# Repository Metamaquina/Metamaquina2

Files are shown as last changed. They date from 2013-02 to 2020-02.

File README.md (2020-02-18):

Metamaquina2
============

Metamaquina 2 - fully parametric 3D printer

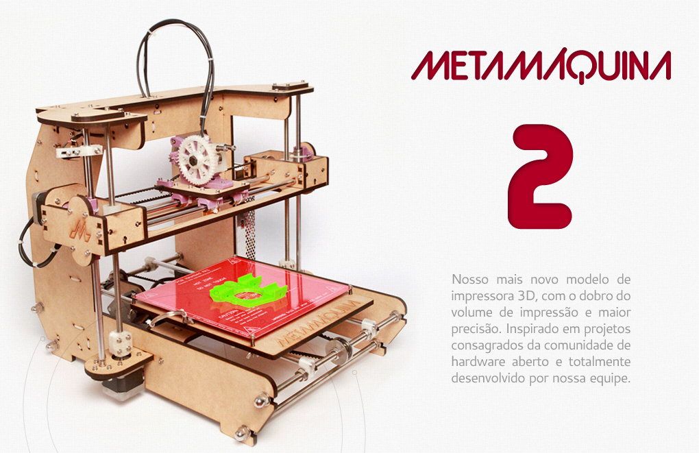
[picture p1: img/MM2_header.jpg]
A photo of the Metamaquina 2 desktop 3d printer


Manufacturing Instructions
==========================

This is a 3d printer project that is completely designed using the parametric CAD tools
 provided by OpenSCAD. In order to deal with this source code you'll need to install OpenSCAD,
following the instructions at: www.openscad.org

The main structure of the machine is built using lasercut MDF panels. The curves for lasercutting 
can be exported to DXF by rendering the lasercutter_6mm_MDF.scad file. Open it in OpenSCAD, press F6 (to compile) and then click Design->Export DXF. The resulting DXF file can be used to cut 6mm thick MDF sheets (or you can change the thickness in the source if you plan to work with some other materials but be sure to review the 3d model in this case since some parts of the design depend on 6mm thickness).

There is also a panel for lasercutting 2mm acrylic to cover the electronics PCB and a panel for lasercutting 5mm acrylic for the ZMAX/ZMIN endstop holders and a couple of 5mm spacers for the LCExtruder. There can be generated from the lasercutter_2m_acrylic.scad and lasercutter_5m_acrylic.scad, respectively. 

Laser Cutter Panel #1
Laser Cutter Panel #2
Laser Cutter Panel #3

The complete 3D model of the machine is described by the Metamaquina2.scad file. Open is in 
OpenSCAD and press F5 to render it.

An OpenSCAD rendering of the Metamaquina 2 desktop 3d printer

Hacking the code
================
Feel free to send us pull requests at https://github.com/Metamaquina/Metamaquina2
 if you make any change to this design that you consider worth sharing with us.

happy hacking,

Felipe Sanches

R&D director at Metamaquina.com.br

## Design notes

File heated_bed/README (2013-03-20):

This is a heated bed design developed in KiCAD.

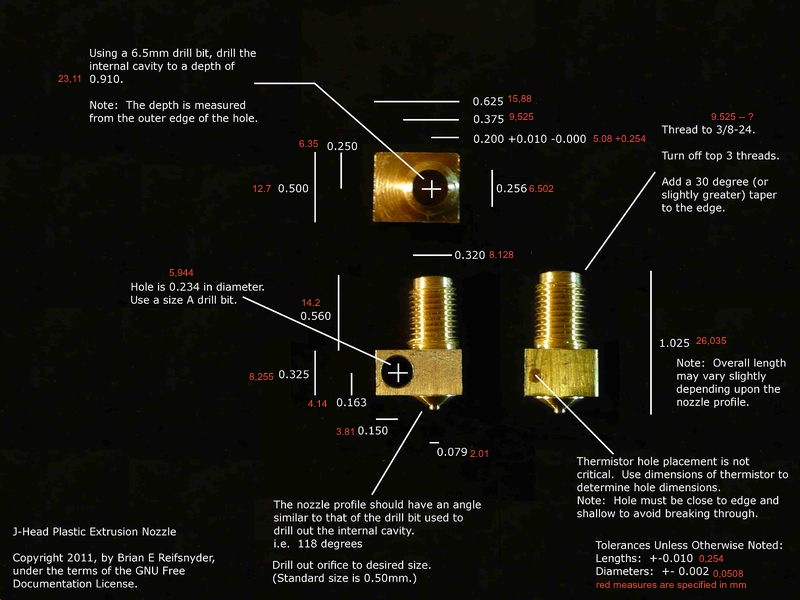
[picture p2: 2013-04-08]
doc/Jhn_md_brass_heater_nozzle.jpg

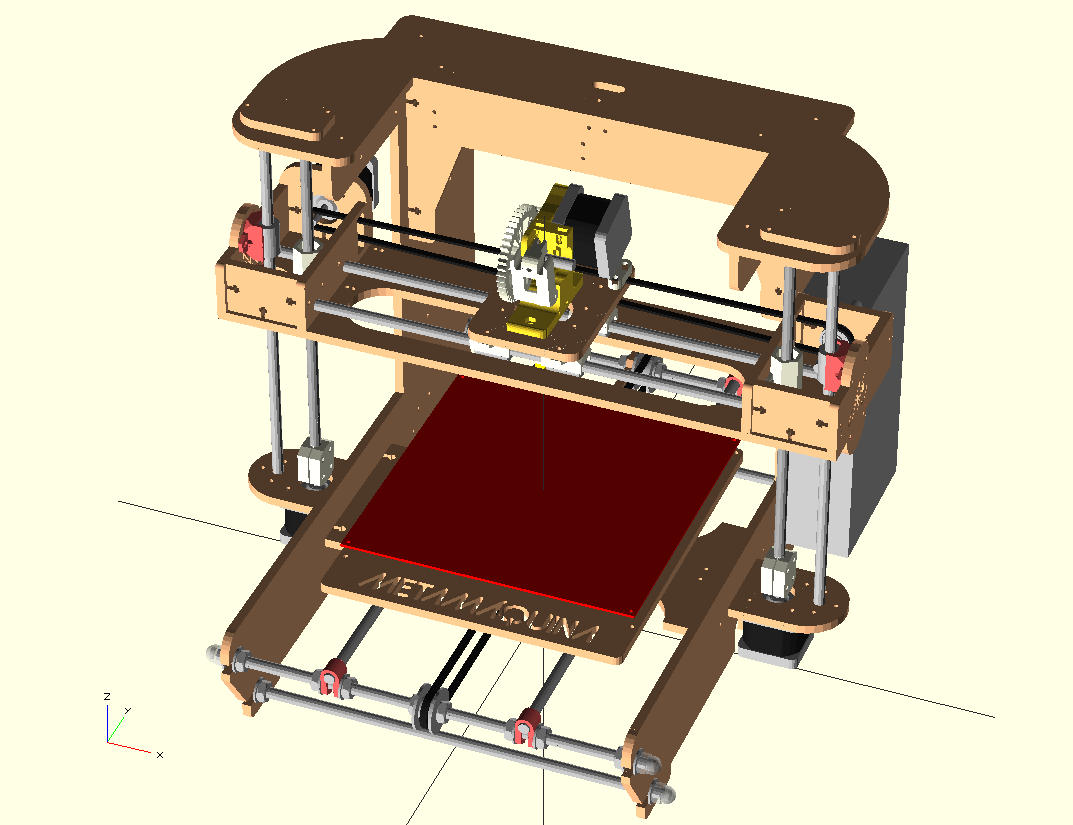
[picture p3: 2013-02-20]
img/MM2.png

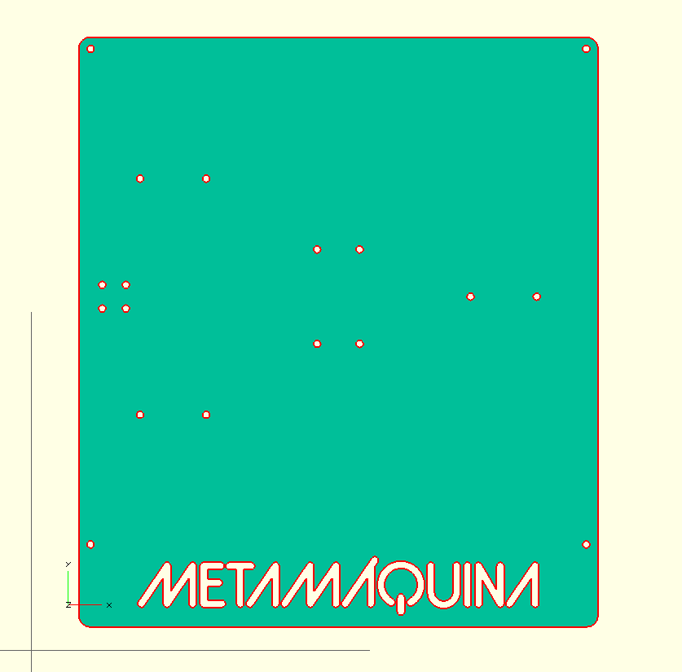
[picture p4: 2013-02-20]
img/lasercutter_panel3.png

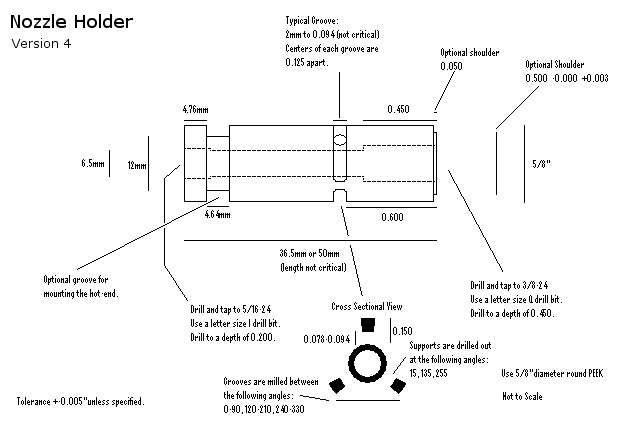
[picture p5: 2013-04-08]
doc/Jhn_nozzle_holder_v4.jpg

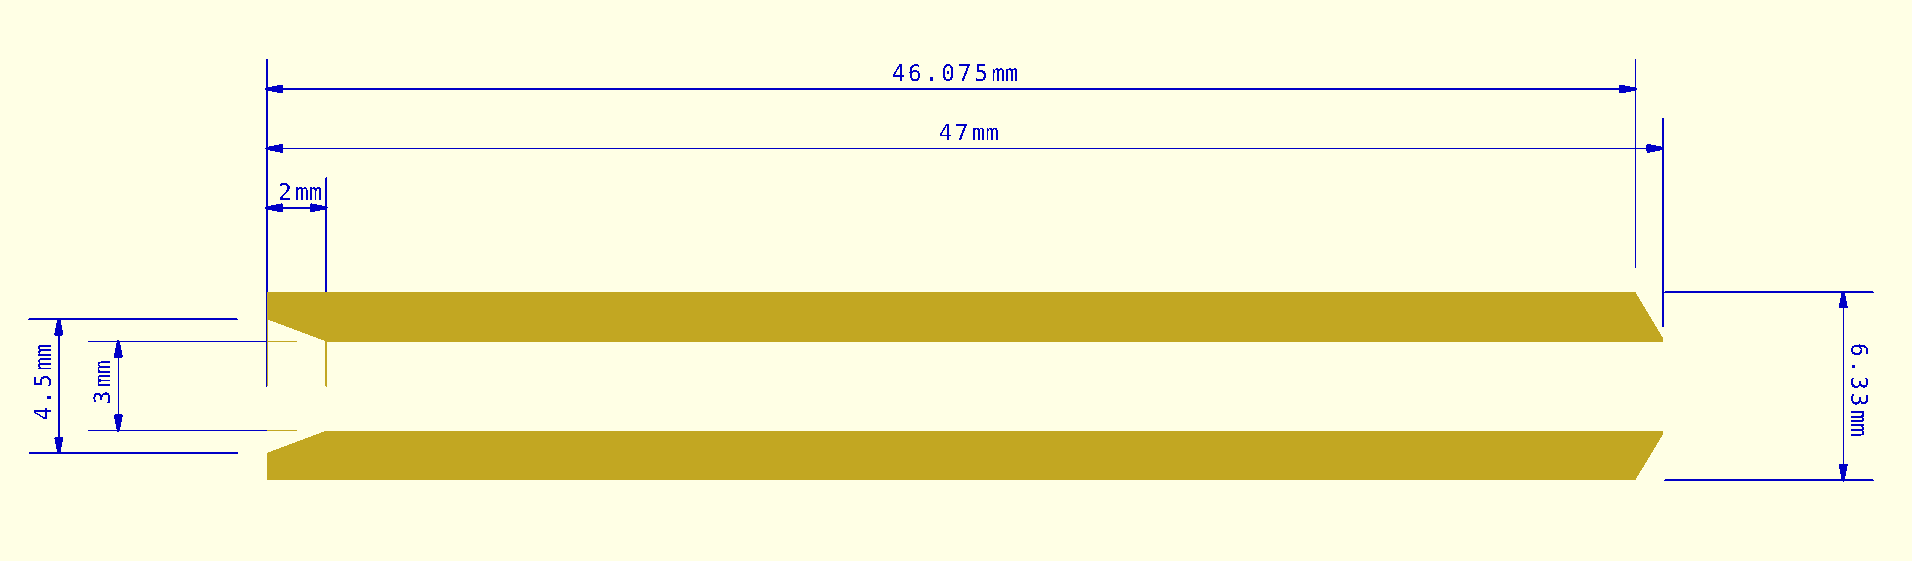
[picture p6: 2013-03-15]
doc/ptfe_liner.png

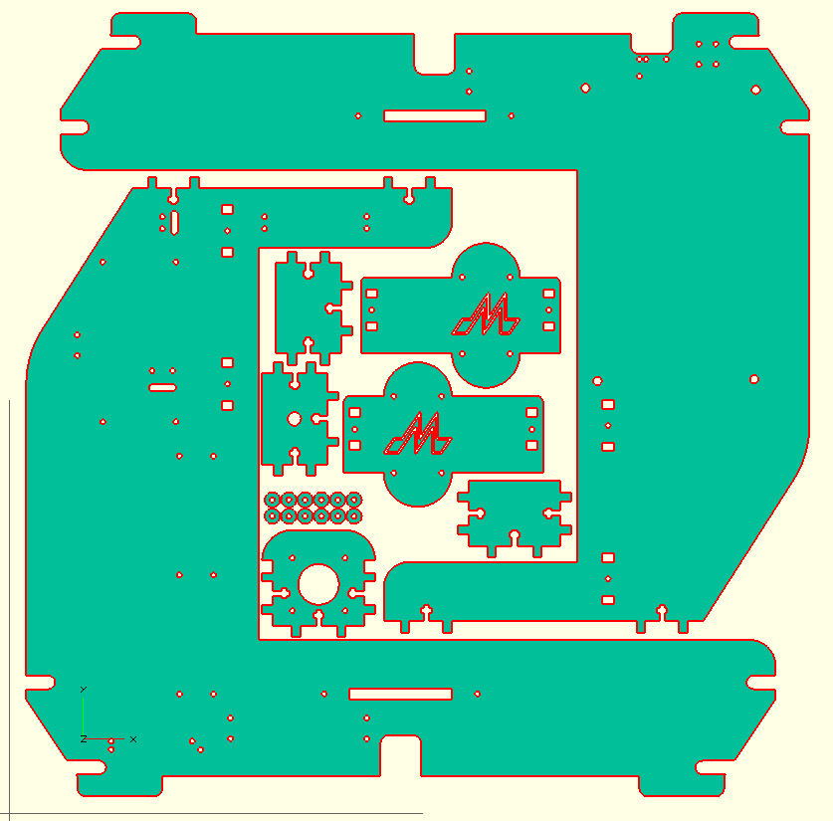
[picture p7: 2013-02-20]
img/lasercutter_panel1.png

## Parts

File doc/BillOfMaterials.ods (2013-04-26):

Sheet: Peças metálicas
Metamáquina 2 – Bill Of Materials |  |  |  | Incomplete
Peças metálicas |  | Local | Quantidade
Barras
 | Lisas M8 | eixo X (420 mm) | 2
 |  | eixo Y (442 mm) | 2
 |  | eixo Z (309 mm) | 2
 |  | Total | 6
 | Roscadas M8 | eixo Z (285 mm) | 2
 |  | Horizontais (309 mm) | 4
 |  | Total | 6
Rolamentos
 | LM8UU | carro X | 4
 |  | carro Y | 3
 |  | X-end idler | 2
 |  | X-end motor | 2
 |  | Total | 11
 | 608ZZ
 |  | Total
Parafusos
 |  | Total | 0
Motores
 | Motor de passo NEMA 17 2,5 kgf |  | 5
 |  | Total | 5
Porcas
 | M2.5 mm |  | 2
 |  | Total
 | M3
 |  | Total | 0
 | M3 locknut
 |  | Total | 0
 | M4
 |  | Total | 0
 | M8
 |  | Total | 0
 | M8 locknut
 |  | Total | 0
 | M8 cap nut
 |  | Total | 0
Molas
 |  | Total | 0
Arruelas
 | M3
 | M4
 | M8
 |  | Total | 0

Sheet: Peças de madeira
Metamáquina 2 – Bill Of Materials |  |  |  | Incomplete
Peças de madeira |  | Local | Quantidade
Espaçadores
 | Total |  | 50
Plataforma X |  |  | 1
Plataforma Y |  |  | 1
Endstops
 | Z |  | 1
 | Y |  | 2
 | X
 | Total |  | 3
Endstop holder

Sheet: Peças plásticas
Metamáquina 2 – Bill Of Materials |  |  |  | Incomplete
Peças plásticas |  | Local | Quantidade
Bar clamp
 |  | Eixo Y | 4
 |  | Total | 4
Clipes autoadesivos
 | RA6 | Painel esquerdo | 1
 |  | Total | 1
 | RA13 | Painel esquerdo | 7
 |  | Painel direito | 2
 |  | Painel superior | 1
 |  | Painel inferior | 3
 |  | Total | 13
Correias
 | GT2 x 5mm | Eixo X | 1
 |  | Eixo Y | 1
 |  | Total | 2
Engrenagens
 | Grande | Extrusor | 1
 | Pequena | Extrusor | 1
 |  | Total | 2
Z-link
 |  | Eixo Z | 2
 |  | Total | 2

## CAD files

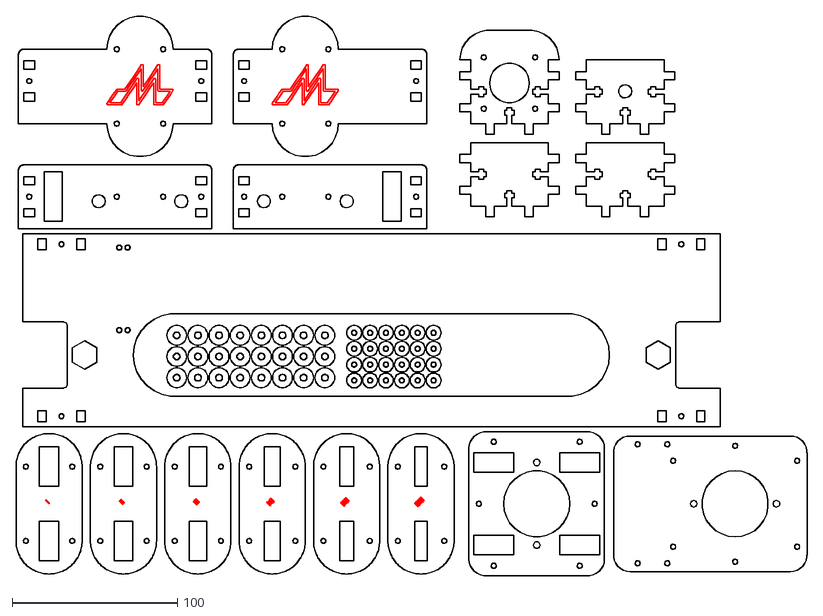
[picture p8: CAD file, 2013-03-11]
dxf/sandwich_test_panel_06Mar2013.dxf
478.5 x 338.4

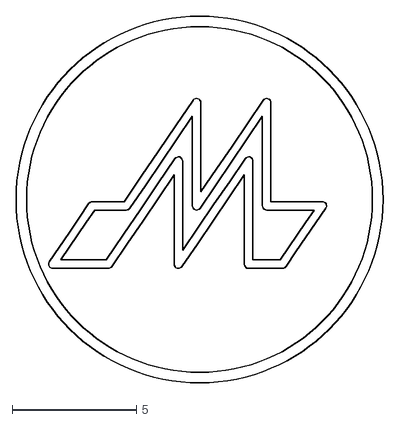
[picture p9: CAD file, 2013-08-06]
M_circle.dxf
14.8 x 14.8

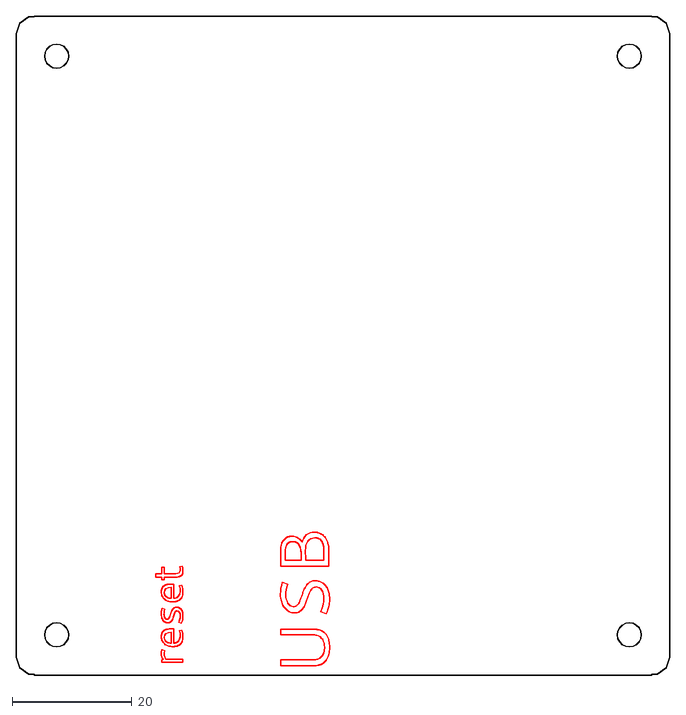
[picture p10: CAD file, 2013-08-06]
lasercutter_2mm_acrylic.dxf
109.0 x 110.0

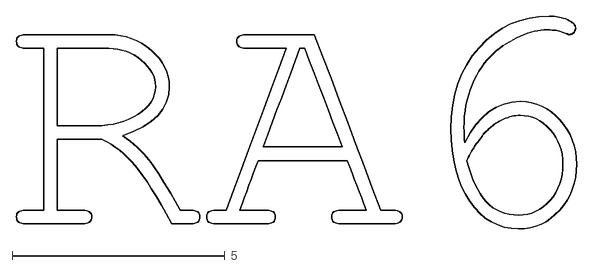
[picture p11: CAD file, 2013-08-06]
RA6.dxf
13.2 x 5.00

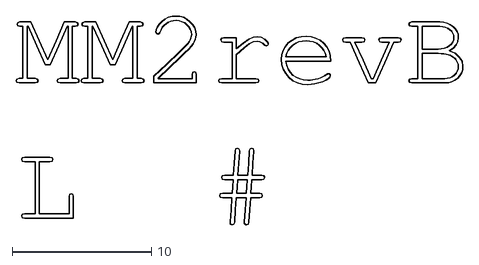
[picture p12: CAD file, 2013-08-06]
serial_number_template.dxf
32.1 x 15.0

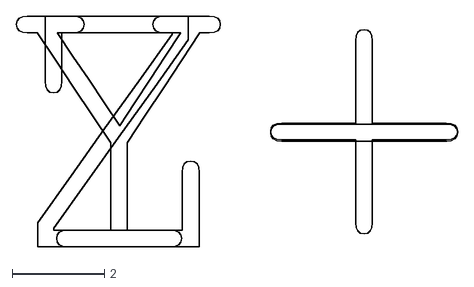
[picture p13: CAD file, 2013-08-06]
labels.dxf
9.56 x 5.00

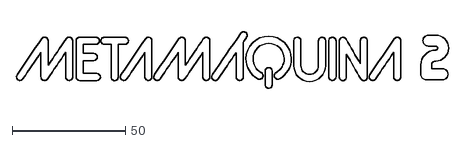
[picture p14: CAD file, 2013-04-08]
metamaquina-2.dxf
191.0 x 24.9

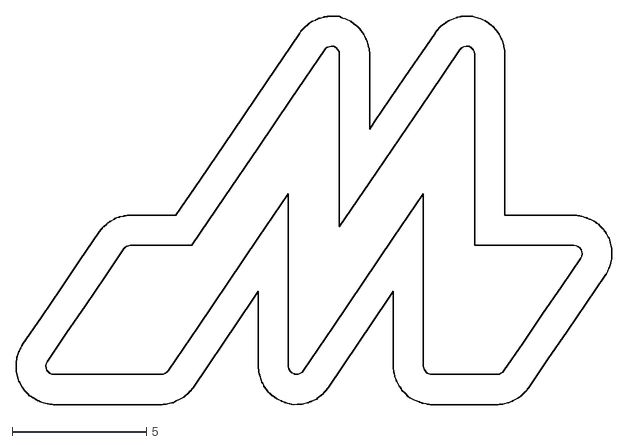
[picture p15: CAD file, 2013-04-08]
MM_hole.dxf
22.2 x 14.4

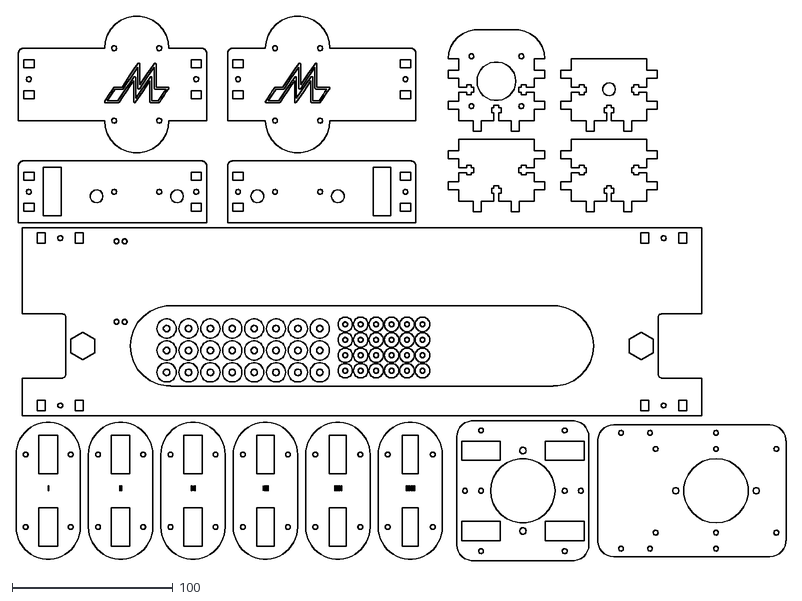
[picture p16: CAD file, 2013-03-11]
sandwich_test_panel.dxf
478.5 x 338.4

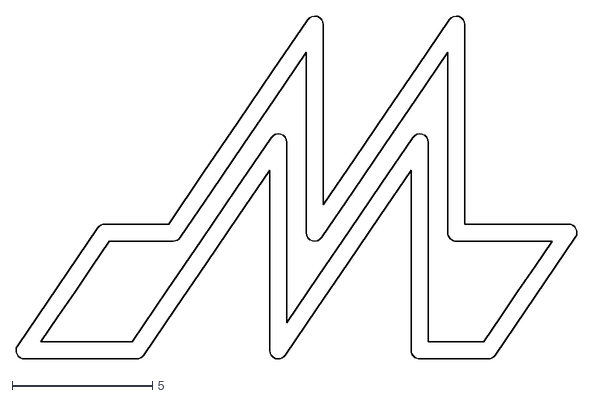
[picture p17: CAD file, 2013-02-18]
MM_logo_small.dxf
20.0 x 12.2

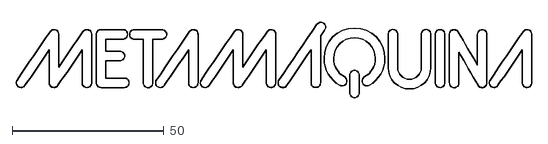
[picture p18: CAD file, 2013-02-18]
metamaquina-170mm_X_25mm.dxf
169.9 x 24.9

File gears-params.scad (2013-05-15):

// (c) 2013 Metamáquina <http://www.metamaquina.com.br/>
//
// Author:
// * Felipe C. da S. Sanches <fsanches@metamaquina.com.br>
//
// This program is free software: you can redistribute it and/or modify
// it under the terms of the GNU General Public License as published by
// the Free Software Foundation, either version 3 of the License, or
// (at your option) any later version.
//
// This program is distributed in the hope that it will be useful,
// but WITHOUT ANY WARRANTY; without even the implied warranty of
// MERCHANTABILITY or FITNESS FOR A PARTICULAR PURPOSE.  See the
// GNU General Public License for more details.
//
// You should have received a copy of the GNU General Public License
// along with this program.  If not, see <http://www.gnu.org/licenses/>.

gear_thickness = 10;

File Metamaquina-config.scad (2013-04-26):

/*Thickness of acrylic or plywood sheets to use.*/
thickness = 6; //millimiters

/*This value is added to the thickness value when drawing cuts for connecting perpendicular sheets together*/
slot_extra_thickness = 0.5;

module TSlot_holes(width=50){
  t_slot_holes(width=width, thickness=thickness+slot_extra_thickness);
}

module TSlot_joints(width=50){
  t_slot_joints(width=width, thickness=thickness, joint_size=5);
}

/*z motor placement in the original Prusa was on top. Our design uses the z motors in the bottom of the machine, but if you want them on top, you can set this variable to true. */
zmotors_on_top = false;

/* Desired build volume: */
BuildVolume_X=200;
BuildVolume_Y=200;
BuildVolume_Z=150;

//rendering configs:
render_lasercut=true;
render_pcb=true;
render_ABS=true;
render_PLA=true;
render_metal=true;
render_threaded_metal=true;
render_rubber=true;
render_peek=true;
render_nylon=true;
render_acrylic=true;

render_nozzle=true;
render_powersupply=true;
render_calibration_guide = false;
render_build_volume=false;
render_xplatform=true;
render_bolts = false; //work-in-progress
render_extruder = true;

//Colors
dark_green = [0,0.2,0];
rubber_color = [0.1, 0.1, 0.1];
nozzle_color = "gold";
pcb_color = [1.0, 0.0, 0.0];
threaded_metal_color = [0.6, 0.6, 0.6];
metal_color = [0.7, 0.7, 0.7];
powersupply_color = metal_color;
PLA_color = [0.95, 0.35, 0.35];
ABS_color = [0.95, 0.95, 0.85];
//sheet_color = [0.95, 0.8, 0.65];
sheet_color = [227/230, 190/230, 151/230];
//sheet_color = [0.9, 0.3, 0.3, 1];
peek_color = "beige";
dark_grey = [0.3, 0.3, 0.3];
green_plastic_color = [0.7,0.8,0,7];
black_plastic_color = [0.3,0.3,0.3];

epsilon=0.1;
inch=25.4;
m25_diameter = 2.5;
m3_diameter = 3;
m4_diameter = 4;
m8_diameter = 8;

//-------------------------
//RepRap standards:

X_rods_distance = 50;
X_rods_diameter=8;
z_rod_z_bar_distance = 30;
Y_rods_distance = 140;

//-------------------------
extruder_mount_holes_distance = X_rods_distance + 14;
microswitch_holes_distance = 9.4;
endstop_holder_width = 15;//TODO
endstop_holder_height = 8;//TODO

XPlatform_height = 45;

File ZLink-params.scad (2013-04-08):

dx_z_threaded = 14;
ZLink_rod_height = 11*sqrt(3)/2;
Zlink_hole_height = (XPlatform_height-thickness)/3;

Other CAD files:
font.dxf
CalibrationRules-conf.scad
608zz_bearing.scad
CalibrationRules.scad
CalibrationZBars.scad
FilamentSpoolHolder.scad
Metamaquina2.scad
Metamaquina_2_extruders.scad
NEMA-dimensions.scad
NEMA.scad
PTFE_liner.scad
PowerSupply.scad
RAMBo.scad
ZLink.scad
acrilico_5mm.scad
bar-clamp.scad
belt-clamp.scad
bolts.scad
cable_clips.scad
configuration.scad
coupling.scad
detailed_608zz_bearing.scad
domed_cap_nuts.scad
endstop.scad
functions.scad
gears.scad
gears_Bowden.scad
heated_bed.scad
hobbed_bolt.scad
jhead.scad
jheads.scad
large_extruder_gear.scad
lasercut_2_extruders.scad
lasercut_extruder.scad
lasercutter_5mm_acrylic.scad
lasercutter_6mm_MDF.scad
lasercutter_6mm_MDF_CalibrationRules.scad
lasercutter_6mm_MDF_CalibrationZBars.scad
lasercutter_6mm_MDF_SpoolHolder.scad
lasercutter_panel.scad
lasercutter_panel4.scad
lasercutter_panel5.scad
lm8uu_bearing.scad
metric.scad
mm2logo.scad
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

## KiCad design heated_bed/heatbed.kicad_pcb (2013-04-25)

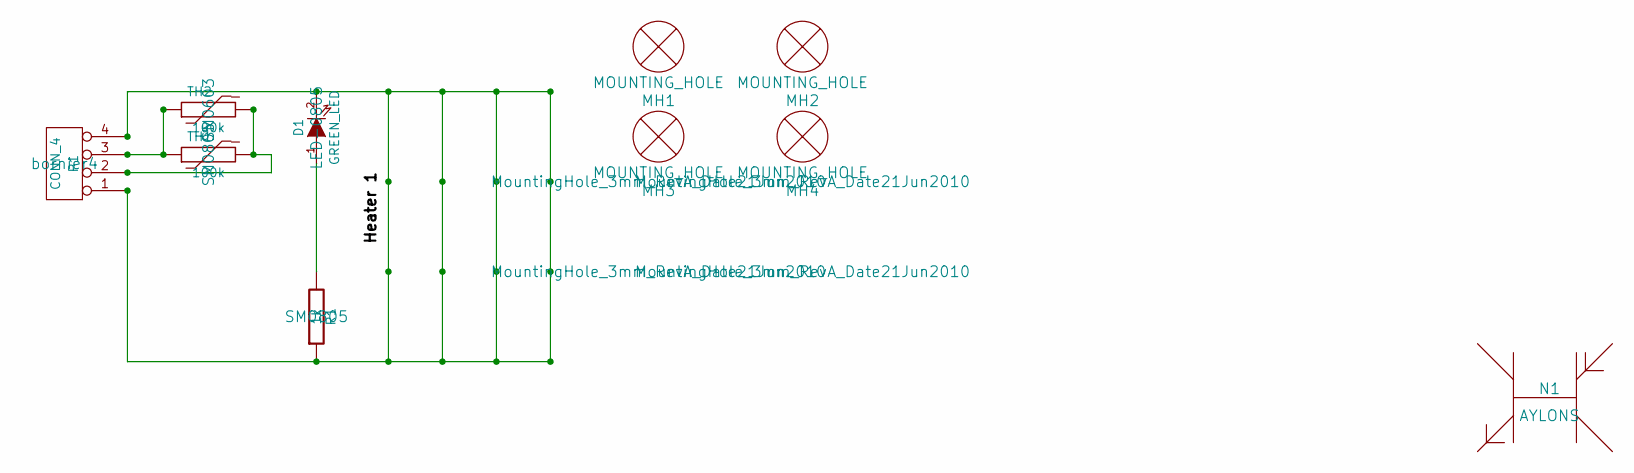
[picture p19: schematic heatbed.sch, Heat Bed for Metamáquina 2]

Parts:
D1: GREEN_LED; LED-0805
MH1, MH2, MH3, MH4: MOUNTING_HOLE; MountingHole_3mm_RevA_Date21Jun2010
N1: AYLONS
P1: CONN_4; bornier4
R1: 1k; SM0805
TH1: 100k; SM0805
TH2: 100k; SM0603

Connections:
unnamed: P1.3, TH1.1, TH2.1
unnamed: P1.2, TH1.2, TH2.2
unnamed: D1.1 (A), R1.2
unnamed: D1.2 (K), P1.1, P1.4, R1.1

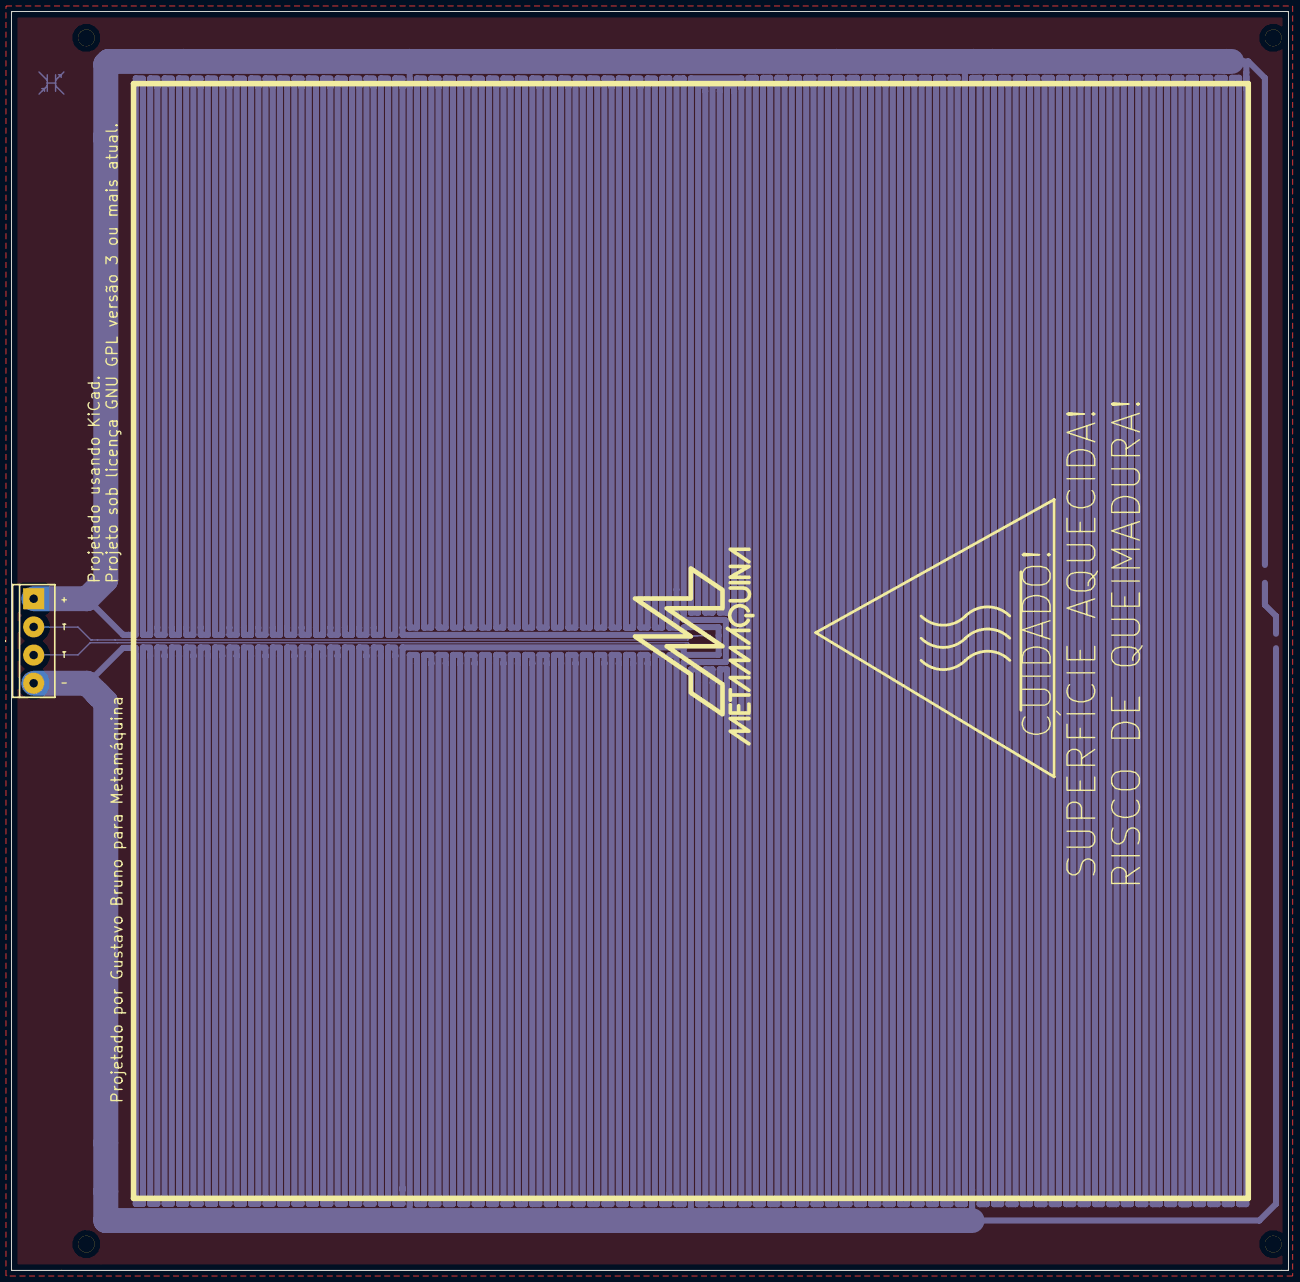
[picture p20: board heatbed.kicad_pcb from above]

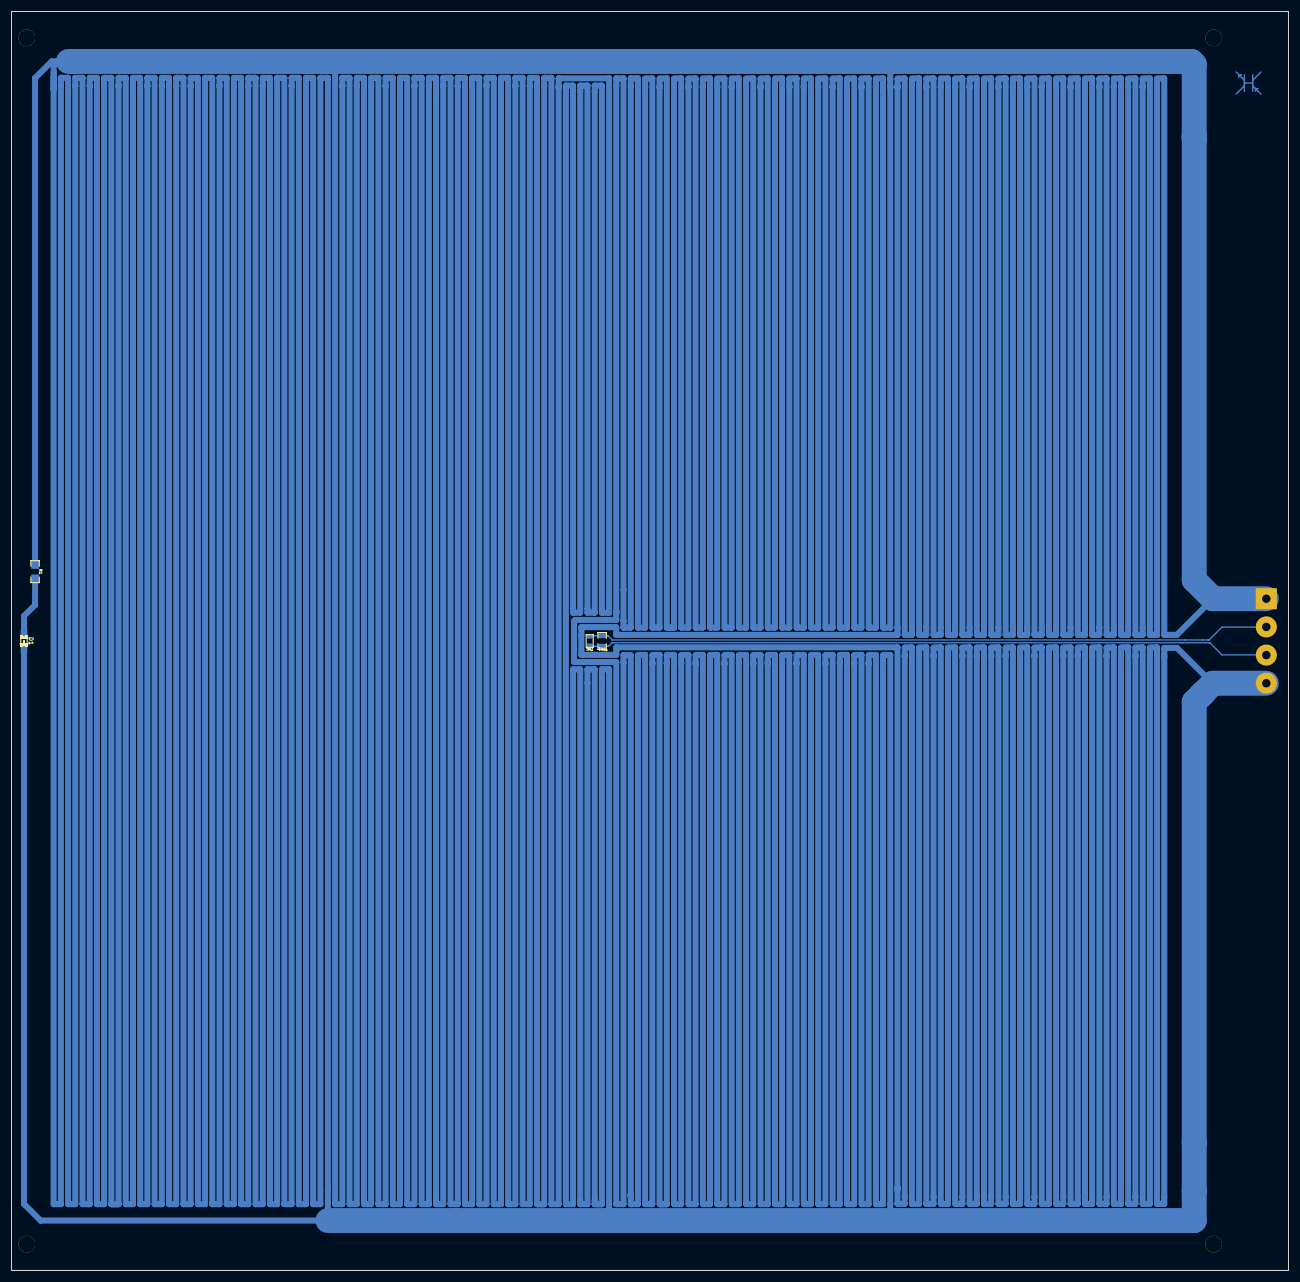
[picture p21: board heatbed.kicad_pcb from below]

Board: 2 copper layers, 230.2 x 227.0 mm, 10 parts (4 on the bottom side), 4 nets.

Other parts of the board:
VAL: MM_logo

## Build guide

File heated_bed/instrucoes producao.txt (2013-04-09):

O funcionamento correto desta placa depende da resistência das suas trilhas. Portanto:

* A placa DEVE ter densidade de cobre de 1oz.
* A placa NÃO deve passar por eletrodeposição ANTES da máscara de solda.

Outras informações:
* Os pads devem ser metalizados por HAL.
* A camada da frente não tem conexão elétrica com nenhuma trilha. Sua função é distribuir calor, portanto a placa deve ser 2 camadas, como nos gerbers.
* Não é necessário metalizar os furos, nem os do conector.

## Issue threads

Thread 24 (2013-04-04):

validar termistor do bico

felipesanches, 2013-04-04:
- Carregar tabela adequada de termistores para o modelo novo de term. e testar de 26 a 240 graus celsius ligado a um bico de extrusão e comparando com o termopar

felipesanches, 2015-02-12:
Tarefa concluída em 2013.

Closed 2015-02-12.

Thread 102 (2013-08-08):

Furo no carro X

rodrigopitanga, 2013-08-08:
O furo para fixação do extrusor no carro X voltado para a parte de trás deve ser uma fenda, e não um furo.

Isso permitirá que o parafuso M4x25 seja fixado na porca antes de o motor ser colocado no bloco extrusor, o que facilitaria muito a montagem do extrusor no carro posteriormente.

felipesanches, 2015-02-12:
foi implementado na revisão D

Closed 2015-02-12.

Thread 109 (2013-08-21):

Bloco extrusor esquenta demais e derrete/esmaga filamento

rodrigopitanga, 2013-08-21:
Causando emplastamento.

Solução: baixar corrente do motor e diminuir pressão na mola do idler.

felipesanches, 2015-02-12:
correção implementada em 2013

Closed 2015-02-12.

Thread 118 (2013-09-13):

Cabeamento do cabeçote extrusor fica muito próximo do motor da extrusora

gui7vaz, 2013-09-13:
Hj coloquei a mão na fiação e não dava nem para encostar o dedo de tão quente.
Isso pode ser um perigo. Vou até fazer um seguro pro meu apartamento.
Soltei um pouco os cabos de modo que eles ficassem bem distantes do motor.

felipesanches, 2015-02-12:
O super-aquecimento dos motores do extrusor foram corrigidos em 2013. Tratava-se de uma configuração errada de corrente do driver de motor de passo.

Closed 2015-02-12.

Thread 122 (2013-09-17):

As peças ficam deformadas na "parte de trás"

gui7vaz, 2013-09-17:
Ando imprimindo algumas coisas e percebi que a parte de trás das peças sempre ficam um pouco deformada. Ontem coloquei a mão na parte traseira da impressora e realmente tinha uma massa de ar quente lá. Hoje farei alguns testes colocando um ventilador virado para o local.

felipesanches, 2015-02-12:
issue duplicada

Closed 2015-02-12.

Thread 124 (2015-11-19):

Dependencia urlgrabber ausente da documentacao

rodrigopitanga, 2015-11-19:
apt-get install python-urlgrabber

felipesanches, 2015-11-19:
Tenho a impressão de que você cadastrou essa issue no repositório errado. Me parece que você queria ter cadastrado isso no repo do Pronterface / Printrun

felipesanches, 2015-11-19:
de qualquer modo, consertei isso no README.md do nosso Printrun agora (no branch mm2)

rodrigopitanga, 2015-11-19:
Ok. Precisa consertar na doc do site tb.

Em 19 de novembro de 2015 18:13:03 BRST, "Felipe Corrêa da Silva Sanches" <notifications@github.com> escreveu:
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

--
Sent from my Android device with K-9 Mail. Please excuse my brevity.

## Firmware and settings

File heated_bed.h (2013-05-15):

// (c) 2013 Metamáquina <http://www.metamaquina.com.br/>
//
// Author:
// * Felipe C. da S. Sanches <fsanches@metamaquina.com.br>
//
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
use <heated_bed.scad>;

heated_bed_pcb_thickness = 2;
heated_bed_pcb_width = 227;
heated_bed_pcb_height = 224;
heated_bed_glass_thickness = 3;

glass_w=heated_bed_pcb_width;
glass_h=200; //TODO

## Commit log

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2013-02-18 Adding a volumetric representation of the space taken by the RAMBo electronics.
    [Metamaquina2.scad]
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2013-02-19 calculate machine dimentions based on the actual desired max build volume (previously we were using the heated bed pcb dimensions as our reference parameter)
    [Metamaquina2.scad]
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2013-02-19 tweak RAMBo y position to align to the top of the power supply
    [Metamaquina2.scad]
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2013-02-21 Initial commit for heatbed hardware design.
    Created schematics, associated components to its footprint (dummy in case of PCB traces and undecided footprints) and generated a PCB layout file.
    [heatbed.sch]
2013-02-21 Created Kicad project and designed the first schematic for the heated bed. Also, associated componentes with footprints (dummy in some cases) and generated the board layout file.
    [heatbed.sch]
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2013-02-27 3d model / 2d drawing of the PTFE liner for our hotend
    [PTFE_liner.scad]
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2013-03-04 Feita a primeira metade da PCB, com duas trilhas de aquecimento prontas. Restam as duas trilhas com menos interferencia externa
    [heatbed.kicad_pcb, heatbed.sch]
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2013-03-06 test panel sent to prototyping on the laser cutter on march 6th 2013 purpose: to validate the bearing sandwich design pattern and to choose the best value for the sandwich_tightening parameter
    [Metamaquina2.scad, sandwich_test_panel.dxf, sandwich_test_panel_06Mar2013.dxf]
2013-03-06 source code for the test panel mentioned in the previous commit message
    [sandwich_test_panel.scad]
2013-03-07 invert position of ybearings to avoid hitting the ymotor
    [Metamaquina2.scad]
2013-03-08 Removing 3d printable wade extruder from the design. We'll try using an extruder based on the Printrbot one, so that we can lasercut it.
    [MM_wade-large.stl, Metamaquina2.scad, gregs_wade.scad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]
2013-03-08 Adding LaserCut Extruder design implemented in SolidPython. This design is basically the same as the Printrbot extruder.
    [extruder-printrbot-layers.dxf]
2013-03-08 moving the extruder files to the base directory to avoid openscad bug when referencing external DXF files.
    [extruder-printrbot-layers.dxf]
2013-03-08 fixing python code to use new solid python module name
    [lasercut_extruder.scad]
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2013-03-08 fix ptfe liner model
    [PTFE_liner.scad, hobbed_bolt.scad, technical_drawing.scad]
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2013-03-11 fixing ptfe liner technical drawing (angle = 118 degrees)
    [PTFE_liner.scad]
2013-03-11 - fix rodends (the machine got slightly smaller in the X direction, so the RodEnds needed minor tweaks to fit) - removed 1 bolt from each bottom rodend - removed 2 unused holes for each of the top ro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
    [Metamaquina2.scad]
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2013-03-11 moving RAMBo positioning a bit closer to the edge of the sidepanel
    [Metamaquina2.scad]
2013-03-12 Moving RAMBo specific declarations to a RAMBo.scad file and also creating a separate Metamaquia-config.scad file for general configuration of the model.
    [Metamaquina-config.scad, Metamaquina2.scad, RAMBo.scad]
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2013-03-12 - refactoring of belt rendering code - belts can now be placed around an arbitrary number of bearings
    [Metamaquina2.scad]
2013-03-12 Moving the ZMotors 5 millimiters down in order to free some space for the heads of the bolts in the YPlatform LM8UU bearing sandwiches.
    [Metamaquina2.scad]
2013-03-12 fix rendering of belt clamps
    [Metamaquina2.scad, belt-clamp.scad]
2013-03-12 - fix kerf for tslots - tslots refactoring for better code legibility/maintainance
    [Metamaquina-config.scad, Metamaquina2.scad, tslot.scad]
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2013-03-12 mirroring on of the frontal Xend sheets in the laser cutter panel so that the laser burnt side ends up turned to the same side (eighter exterior or interior) for both XEnds
    [lasercutter_panel2.scad]
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2013-03-12 Based on the tests performed on our bearing sandwich prototypes, the ideal bearing_tightening parameter seems to be 1mm, so that's what we'll use.
    [Metamaquina2.scad]
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2013-03-13 XCarriage: fixing placement of hexspacers and adding 5th and 6th hexspacer
    [Metamaquina2.scad]
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2013-03-13 fixing header and adding a comment
    [lasercutter_panel4.scad]
2013-03-15 Removing SolidPython implementation of the LaserCutExtruder. Instead, this time well stick to a pure OpenSCAD implementation.
    [Metamaquina2.scad, lasercut_extruder.scad]
2013-03-15 - extracting out NEMA specific scad code to an external file - adding a motor to the extruder model
    [Metamaquina2.scad, NEMA-dimensions.scad, NEMA.scad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]
2013-03-15 adding gears from thingiverse - we'll try using these in our extruder
    [TZ_Huxley_extruder_gears.scad, TZ_Huxley_extruder_huge_gear.stl, TZ_Huxley_extruder_motor_gear.stl]
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2013-03-18 adding a structural enforcement to the extruder slices that have a bearing slot
    [lasercut_extruder.scad]
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2013-03-18 trying to fix the dimensions for hobbed-bolt holes in the large extruder gear
    [TZ_Huxley_extruder_gears.scad]
2013-03-20 trying to reduce the length of the bolts that hold springs in the lasercut extruder
    [lasercut_extruder.scad]
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2013-03-20 tweaking the idler back_face shape in order to free space for the extruder gear
    [lasercut_extruder.scad]
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2013-03-21 Fixing typo in the copyright header of several files
    [608zz_bearing.scad, Metamaquina2.scad, NEMA.scad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]
2013-03-22 minor fix on the extruder gear scad source (height variable was not defined)
    [TZ_Huxley_extruder_gears.scad]
2013-03-22 adding tightening parameter to the small bearing sandwich used in the YPlatform
    [Metamaquina2.scad]
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2013-03-25 make top hole for threaded rods larger to avoid whobble
    [Metamaquina2.scad]
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2013-03-26 fix undefined color name
    [RAMBo.scad]
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2013-03-27 larger zmotor central hole to let the coupling pass through the hole
    [Metamaquina2.scad]
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2013-03-27 refactoring ZLink and modifying holes placement so that it's impossible to mount it in a wrong position.
    [Metamaquina-config.scad, Metamaquina2.scad, ZLink.scad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]
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2013-03-31 Moving the XZStage 2 centimeters closer to the front of the macihne in order to get more space for the RAMBo electronics & for the power supply.
    [Metamaquina2.scad]
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2013-03-31 fliping positioning of the sheets for YMIN and YMAN endstops to avoid hitting the YMotor
    [Metamaquina2.scad]
2013-04-01 fix placement of parts in lasercut panels
    [lasercutter_panel1.scad]
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2013-04-01 adding missing file previously uncommitted
    [ZLink-params.scad]
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2013-04-05 Subindo arquivos de documentacao do nozzle:
    new file: Jhn_nozzle_v4.scad
    TODO: Verificar se bate com a imagem. Precisa traduzir medidas para mm.
    new file: doc/Jhn_md_brass_heater_nozzle.jpg
    TODO: Atualizar furo do termistor e ver se bate com scad
    new file: doc/Jhn_nozzle_holder_v4.jpg
    TODO: atualizar para modelo do Rui
    [Jhn_nozzle_v4.scad]
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2013-04-08 changing variable name (because I had chenged it before but not everywhere)
    [endstop.scad]
2013-04-08 Fixing motor gear model.
    [TZ_Huxley_extruder_gears.scad]
2013-04-08 Fixing barclamp model assymmetry.
    [bar-clamp.scad]
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2013-04-08 fixing TABs -> 2 spaces
    [bar-clamp.scad]
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2013-04-09 fixing colors and bringing back the nozzle model rendering to the main machine model
    [Metamaquina-config.scad, Metamaquina2.scad, RAMBo.scad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]
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2013-04-09 removing default "hull"-shaped hole from ZLink (keep it optional as a parameter)
    [ZLink.scad]
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2013-04-09 fixing value of distance between microswitch mount holes
    [Metamaquina-config.scad, lasercutter_panel3.scad]
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2013-04-09 fix dimensions of the Yplatform_sheet
    [Metamaquina2.scad]
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2013-04-19 Fixing the build. There were semi-colons missing in the end of 2 statements.
    [Metamaquina2.scad]
2013-04-19 fix issue #35 https://github.com/Metamaquina/Metamaquina2/issues/35
    [lasercut_extruder.scad]
2013-04-19 Fix Issue #34
    [Metamaquina2.scad]
2013-04-22 Fix issue #31: Adding holes for extruder wires in the top of the LCExtruder.
    [lasercut_extruder.scad]
2013-04-22 fix issue #37
    [lasercut_extruder.scad]
2013-04-22 moving xcarriage curve a bit in the lasercutter panel to avoid overlap with another part
    [lasercutter_panel2.scad]
2013-04-22 fix issue #47 : Repositioning YEndstops to conform to the nominal travel of 20 centimeters.
    [Metamaquina2.scad, lasercutter_panel2.scad]
2013-04-22 fix issue #46 : Add ZMIN/ZMAX holders to a lasercutter panel
    [lasercutter_panel3.scad]
2013-04-22 fix issue #40 : Adding ZMIN to the model (including adjustable mount holes)
    [Metamaquina2.scad, endstop.scad]
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2013-04-23 fix mount holes for ZMIN/ZMAX endstops
    [Metamaquina2.scad]
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2013-04-24 corrigindo erro no roteamento da heated bed que causava um curto entre uma das trilhas do termistor e uma das trilhas de aquecimento
    [heatbed.kicad_pcb]
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2013-04-26 Inverting small gear (better for printing).
    [small_extruder_gear.scad]
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2013-04-26 updating the heated bed outline for lasercutting
    Also adding an utils.scad file with a module that will help me make cuts in the edges of lasercut sheets.
    [Metamaquina2.scad, utils.scad]
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2013-04-26 Adding connector details to the NEMA17 model and rotating the motors to serve as machine build documentation
    [Metamaquina2.scad, NEMA.scad]
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2013-04-26 fix issue #58 : make sure every motor has a ziptie for holding its wires in place
    [Metamaquina2.scad]
2013-04-26 Enlarging extruder wires hole on top panel face (so it fits the motor wire connector).
    [Metamaquina2.scad]
2013-04-26 fix issue #54 : Adding in sidepanel hole for XMotor wire
    [Metamaquina2.scad, NEMA-dimensions.scad]
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2013-04-27 adding file that was missing in a previous commit: heated_bed.scad
    [heated_bed.scad]
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2013-04-29 fix issue #52 : Make sure wires and connectors can be routed through holes for the ZMAX/ZMIN/YMAX/YMIN endstop switches
    [Metamaquina2.scad, endstop.scad, utils.scad]
2013-04-29 wip: issue #51 (YMIN/YMAX spacers)
    [Metamaquina2.scad, endstop.scad]
2013-04-29 fix issue #51 : YMIN/YMAX spacers also some good refactoring of endstop descriptions
    [Metamaquina2.scad, endstop.scad, lasercutter_panel3.scad]
2013-04-29 fix YCarPosition coordinate calculation and comment out XYZ CarPosition animation routines.
    [Metamaquina2.scad]
2013-04-29 fix issue #57 : ziptie holes for RAMBo wires
    [Metamaquina2.scad, RAMBo.scad]
2013-04-29 Fix issue #59 : One single panel with everything that needs to be lasercut for manufacturing one 3d printer
    [lasercutter_panel.scad]
2013-04-30 fix issue #53 : update heatedbed wiring holes
    [Metamaquina2.scad]
2013-04-30 fix issue #55 : enlarge beltclamps so that they are stronger when lasercut
    [Metamaquina2.scad, belt-clamp.scad, lasercutter_panel.scad]
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2013-05-02 fix issue #64 : edge cuts for preassembled YMAX/YMIN wiring
    [Metamaquina2.scad, endstop.scad]
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2013-05-02 fix issue #73: reduce the length of XMIN/XMAX endstop holder "wing"
    [Metamaquina2.scad]
2013-05-02 fix issue #65 : Mirror ZMIN lasercut outlines
    [endstop.scad]
2013-05-02 fix issue #66 : adding heated bed glass to the model and some refactoring to the heated bed code
    [Metamaquina2.scad, heated_bed.scad]
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2013-05-02 fix issue #85 : wiring holes for the beated bed
    [Metamaquina2.scad]
2013-05-02 fix issue #63 : updating cable clip sizes
    [Metamaquina2.scad, cable_clips.scad]
2013-05-02 fix issue #69 : positioning of the safety ZMIN endstop
    [Metamaquina2.scad, endstop.scad, utils.scad]
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2013-05-03 fix issue #84 : reposition zipties for extruder wires
    [lasercut_extruder.scad]
2013-05-03 fix heated bed / build platform z coordinates calculation
    [Metamaquina2.scad]
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2013-05-03 Additional parts for tightening up the TopPanel extruder wiring hole.
    [Metamaquina2.scad]
2013-05-03 fix: extra zmin area in the sidepanel was obstructing part of the bottompanel slot
    [Metamaquina2.scad]
2013-05-03 avoid collision in lasercut_extruder panel and fix rendering of yplatform_face in the lasercutter_panel
    [lasercutter_panel.scad]
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2013-05-03 avoid colision between xend_bearing_face and extra area for ZMIN in the sidepanel
    [lasercutter_panel.scad]
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2013-05-21 fixing positioning (height) of RAMBo pcb and acrylic cover
    [RAMBo.scad]
2013-05-21 fix size of the hole for passing the zmax microswitch
    [endstop.scad]
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2013-05-22 fixo positioning of a tslot shape in the power supply box
    [PowerSupply.scad]
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2013-05-23 re-enabling rendering of all materials (disabled by mistake in previous commit)
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2013-05-26 fix calculation of calibration measures (to consider tslot holes' clearance)
    [Metamaquina2.scad]
2013-05-27 Avoiding collision of the frontal Y Endstop Tab with the frontal threaded rod. Adding bolts to the sandwich faces of the yplatform so that we can lift up the MachineBottomPanel to avoid friction of t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
    [Metamaquina2.scad, bolts.scad]
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2013-06-07 fixing dimensions of mount holes for the onoff switch and for the powersupply female connector
    [PowerSupply.scad]
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2013-06-07 fixing BOM item (extruder idler: "threaded rod" => "smooth rod")
    [lasercut_extruder.scad]
2013-06-07 correction of ymin/ymax mount holes
    [endstop.scad]
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2013-06-07 inclusion of side parts and correction of the top hole
    [FilamentSpoolHolder.scad, Metamaquina2.scad]
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2013-06-13 moving the rectangular zmax mount hole a few millimiters down so that it does not get too close to the top border of the sidepanel
    [endstop.scad]
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2013-06-13 mirroring faces in the laser cutter panel for aestethical purposes regarding the burnt side
    [lasercutter_panel.scad]
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2013-06-14 tightening a bit the holes for X & Z smooth rods
    [Metamaquina2.scad]
2013-06-14 clearance in the PSU-box front and back faces to deal with variations in the dimentions of parts supplied by the PSU manufacturer
    [PowerSupply.scad]
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2013-06-14 fix positioning of tslot mount holes for the PSU box
    [PowerSupply.scad]
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2013-06-14 fixing positioning of the small Y Sandwich face in the lasercutter plate
    [lasercutter_panel.scad]
2013-06-14 changing mount position of the small y_bearing_sandwich to reduce the risk of getting the heated bed wiring stuck in it
    [Metamaquina2.scad]
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2013-06-14 fixing positioning of ymax/ymin labels
    [endstop.scad]
2013-06-14 adding a label to the RA6 mount place to avoid mistakes during manufacturing
    [RA6.dxf, cable_clips.scad]
2013-06-14 fixing calibration math
    [Metamaquina2.scad]
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2013-07-03 retired the tab from the rear rule and changed the wrong print of the rear bar
    [CalibrationRules-conf.scad]
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2013-08-08 Modified BillOfMaterials calls to include part ref. Fixed belt modules naming and belt BOM calls Fix rods and bars size printed in BOM Fixed a few typos and parts naming
    modified: 608zz_bearing.scad
    modified: Metamaquina2.scad
    modified: NEMA.scad
    modified: PowerSupply.scad
    modified: RAMBo.scad
    modified: ZLink.scad
    modified: bar-clamp.scad
    modified: belt-clamp.scad
    modified: bolts.scad
    modified: cable_clips.scad
    modified: coupling.scad
    modified: domed_cap_nuts.scad
    modified: endstop.scad
    modified: heated_bed.scad
    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
    [608zz_bearing.scad, Metamaquina2.scad, NEMA.scad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]
2013-08-08 Idler must have 2 acrylic 5mm spacers to accomodate laser cut error
    [lasercut_extruder.scad]
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2018-01-24 Revert last contribs from sara (#125)
    This places the repo's master branch back into the last working state (as it was used for manufacturing our last batch of Metamáquina 2 3D printers back in 2013). These 4 reverted commits contributed by Sara were experimental things we were working on back then, so we'll keep them in the git history for anyone who might want to take a look at them someday.
    Happy Hacking!
    Felipe Correa da Silva Sanches
    R&D director at Metamáquina
    * Revert "again"
    * Revert "final review of the original Metamaquina2 files"
    * Revert "New files extruders-clamp for our peek extruders-clamp-1 for seemecnc"
    * Revert "creating branch"
    This reverts commits 27b05b87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
    [CalibrationRules-conf.scad, CalibrationRules.scad, CalibrationZBars.scad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]

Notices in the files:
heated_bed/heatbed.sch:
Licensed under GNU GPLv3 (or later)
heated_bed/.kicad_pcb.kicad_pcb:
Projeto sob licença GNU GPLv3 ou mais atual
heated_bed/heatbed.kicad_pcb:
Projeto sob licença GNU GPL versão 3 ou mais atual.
